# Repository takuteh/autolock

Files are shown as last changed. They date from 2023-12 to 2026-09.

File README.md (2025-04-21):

# オートロック

## GPIO など

リセットボタン（未実装）GPIO 27  
リードスイッチ GPIO 3  
開錠ボタン GPIO 9  
施錠ボタン GPIO 2  
サーボモーター（上側）GPIO 19  
サーボモーター（下側）GPIO 6  
モーター電源用リレー　 GPIO 22

## 運用方法・注意事項

<ins>**1.direct_version(鍵・モーター直結型)**</ins>

- 鍵に直接モーターを取り付けて制御する方式である
  ソースは direct_version 以下

- lock.sh を crontab に記述すれば、起動時に実行されるようになる

- main.py を実行すればオートロックが起動するが、sudo で実行する必要がある

- main.py は C 言語で記述された関数を呼び出しているので、C ディレクトリ内のプログラムを使用する

- ferica 登録は　 read_idm.py 　を実行する、その際他のプログラムなどで
  カードーリーダーを使用していると読み取りができないため全て停止させてから
  読み取りを行う

- 読み取られた idm は idm_list.txt に登録され、プログラムもそのリストから読み出す

- idm_list.txt の一行目がなぜか読み取られないので二行目以降に記述

<ins>**2.gear_version(ギアボックス付きの制御機構)**</ins>

- 施錠・解錠を手動でも行えるようにギアボックス付きのオートロックを追加した
  ソースは `gear_version` 以下

- **セットアップ**
  下記コマンドを実行すれば以下の処理や設定が全て行われる

  ```
  cd gear_version
  mkdir build
  cd build
  cmake ..
  make
  cd ..
  sudo setup.sh
  ```

- **依存関係**  
  `pigpio`,`mosquitto`,`libmosquitto-dev`,`libcurl4-openssl-dev`  
  json は[nlohmann/json](https://github.com/nlohmann/json)ライブラリを使用  
  curl は LINE,Slack の API で使用するため、API を使用しない場合は不要

- **実行ファイル**  
  バイナリは`gear_version/bin`に生成される  
  systemd に autolock のプログラムを登録することで自動起動させることができる  
  Unit ファイルは`gear_version/service/autolock.service`である  
  実行プログラムのパスをバイナリのあるディレクトリに修正する必要あり

- **設定関係**  
  `gear_version/etc/autolock_setting.json`で各種設定を行う  
  以下の各項目について設定が可能である

  - メインの動作設定はオートロックの有無効,ドアの開放時の閉ボタンの動作,鍵の回転方向
    未施錠の場合のタイムアウト秒数,施錠までの秒数を設定する,"no"とすれば無制限
  - MQTT は開錠・施錠・リレー制御のトピック、メッセージ、mqtt ポート、ブローカー ip
  - LINE はチャンネルのアクセストークン、送信先ユーザー ID
  - Slack はチャンネルのアクセストークン、送信先のチャンネル名
  - `/etc/mosquitto/mosquitto.conf`を変更し、mqtt のポート設定と外部からのアクセス許可をする必要あり

- **ライブラリ**  
  外部ライブラリとして`nlohmann/json`,`pigpiod_if2`,`mosquitto`  
  独自ライブラリとして`control_servo`,`min_mqtt`,`autolock_setting`,`line_api`,`slack_api`がある、これらはビルドすると`gear_version/lib`内に配置される  
  `line_api`,`slack_api`は LINE と Slack に通知をするライブラリである

- **テストコード**  
  各種テストコードのビルド先はビルドディレクトリの`src/test_code`内  
  `line_test`と`slack_test`はアクセストークンと送信先をソース内を変更して設定する必要がある  
  `gear_version/src/test_code`内にすべてのソースコードがある  
  作者の環境ではラズパイとモーターの電源は別で取っているので、モーターの動作が不安定になった場合に備えリレーで電源を制御している  
  `reray_on`,`reray_off` でそれぞれ電源の入切が可能である

- サーボモーター MG996R の使用を前提としたギアボックスの 3DCAD データ(stl 形式)は 3D_Models 以下にある

- Eagle で作成した基板データは pcb_data 以下にある([説明](https://github.com/takuteh/autolock/blob/main/pcb_data/READMD.md))

- **API**  
  オートロックの内部 API として MQTT を利用している.
  以下の例のように json 形式でブローカーに目的の動作のトピック名を指定し,メッセージ送信を行う．
  
  **フルメッセージ**
  ```
  {"app":"LINE","message":"1","user":"takuteh"}
  ```

  app,user 要素は，それぞれ通知を行う際にどのアプリから制御を行なったか，誰が操作をしたのかを判別することが可能．
  上記の例で`/door/open`トピックに送信すると`「takutehがLINEで開錠しました」`という通知が行われる.message 要素は必須だが，それ以外は指定しなくても動作する.
  
  **最小構成のメッセージ**
  ```
  {"message":"1"}
  ```

  「unknown が MQTT で開錠しました」という通知が行われる.

  **mosquitto での送信例(broker ip 192.168.1.1 の場合)**
  ```
  mosquitto_pub -h 192.168.1.1 -t "/door/open" -m '{"app":"LINE","message":"1","user":"takuteh"}'
  ```

## ディレクトリ構成

※一部省略

<pre>
autolock/
├── 3D_Models
│   └── ...
├── pcb_data
│   └── ...
├── README.md
├── direct_version
│   ├── C
│   │   ├── Makefile
│   │   ├── close.c
│   │   └── open.c
│   ├── C++
│   │   ├── src
│   │   │   ├── auto_lock.cpp
│   │   │   ├── auto_lock.hpp
│   │   │   ├── switch.cpp
│   │   │   └── switch.hpp
│   │   ├── test
│   │   └── test.cpp
│   ├── Python
│   │   ├── direct_lock.service
│   │   ├── main.py
│   │   └── read_idm.py
│   └── README.txt
└── gear_version
    ├── CMakeLists.txt             :全体のビルド用
    ├── etc
    │   └── autolock_setting.json :設定ファイル
    ├── include                 
    │   ├── autolock_setting.h
    │   ├── control_servo.h
    │   ├── line_api.h
    │   ├── min_mqtt.h
    │   └── slack_api.h
    ├── service
    │   └── autolock.service    :systemdのserviceファイル
    ├── setup.sh                 :初回ビルド前に実行するスクリプト
    └── src
        ├── autolock.cpp         :メインのコード
        ├── autolock_setting.cpp :設定ファイルの読込
        ├── control_servo.cpp    :サーボモーター制御
        ├── line_api.cpp         :LINEへ送信する
        ├── min_mqtt.cpp         :MQTT関連の制御・設定
        ├── slack_api.cpp        :Slackへ送信
        ├── test_code            :デバッグ用コード
        │   ├── CMakeLists.txt  :test_codeのビルド用
        │   ├── down_close.c
        │   ├── down_open.c
        │   ├── line_test.cpp
        │   ├── read_sw.cpp
        │   ├── relay_off.cpp
        │   ├── relay_on.cpp
        │   ├── slack_test.cpp
        │   ├── up_close.c
        │   └── up_open.c
        └── wiringPi_ver
            ├── home_close.c
            ├── home_open.c
            └── lock_open.c
</pre>

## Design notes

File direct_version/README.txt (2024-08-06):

このバージョンは鍵に直接サーボモーターを取り付け制御する方式である

- fericaを使った認証をしたいためライブラリの豊富なPythonがメインのコードである
- サーボモーターの制御自体はCで書いたものを呼び出しているのでC内のopen.c close.cそれぞれをopen closeとしてコンパイルしPythonディレクトリにmvすれば実行可能
- C++はPythonをC++に書き直そうとしているが、開発中のため現在は使用していない
- Pythonディレクトリ内のdirect_lock.serviceを/etc/systemd/system以下に配置すれば、direct_lock.serviceとして登録される

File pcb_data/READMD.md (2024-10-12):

# 基板データ
基板データはAutodesk Eagleにて制作

## 使用部品 (BOM)
調達のしやすい部品を使用しましたが、データシート参照の上、要件を満たす部品に変更しても構いません
### 基板実装
- サーボモーター用コネクタ（[B03B-SXH](https://akizukidenshi.com/catalog/g/g117151/)）×2
- その他コネクタ（[B2B-XH-A-2](https://akizukidenshi.com/catalog/g/g112247/)）×8
- ラズパイ用ピンソケット ([FH-2x20SG](https://akizukidenshi.com/catalog/g/g100085/)) ×1 
- トランジスタ ([2SC1815](https://akizukidenshi.com/catalog/g/g117089/))×1
- 抵抗 100kΩ×4
- 抵抗 1kΩ×1
- ダイオード ([1N4148](https://akizukidenshi.com/catalog/g/g100941/))×1
- リレー ([SRD-05VDC-SL-C](https://www.alldatasheet.jp/datasheet-pdf/pdf/1131944/SONGLERELAY/SRD05VDCSLC.html))×1

### その他
- ラズベリーパイ4
- サーボモーター ([MG996R](https://akizukidenshi.com/catalog/g/g112534/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))
※MG996Rは<b>制御角180°</b>の<b>メタルギア版</b>

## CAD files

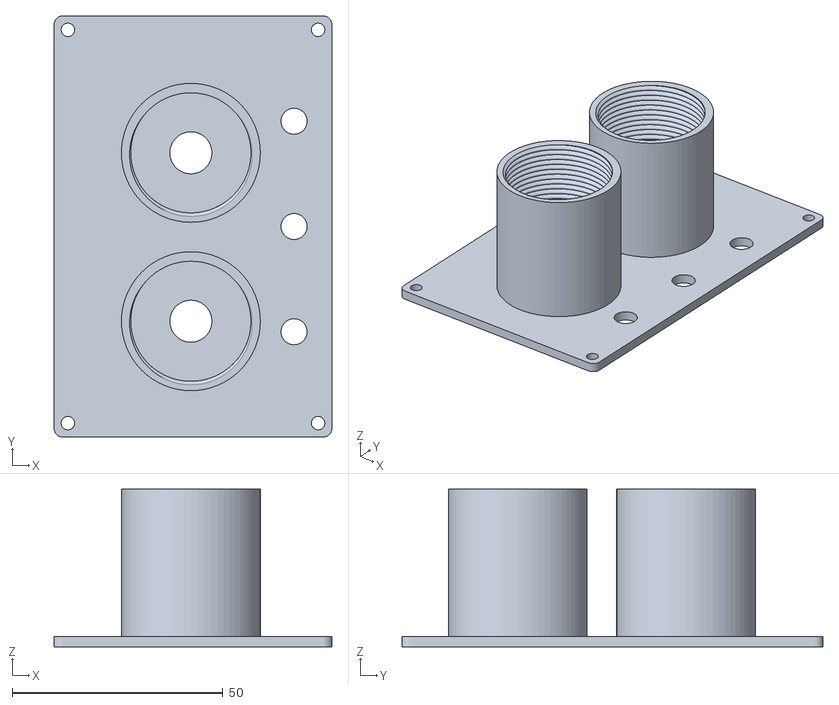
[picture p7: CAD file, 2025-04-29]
3D_Models/RaspiCase_Lid.stl
66.0 x 100.0 x 37.5

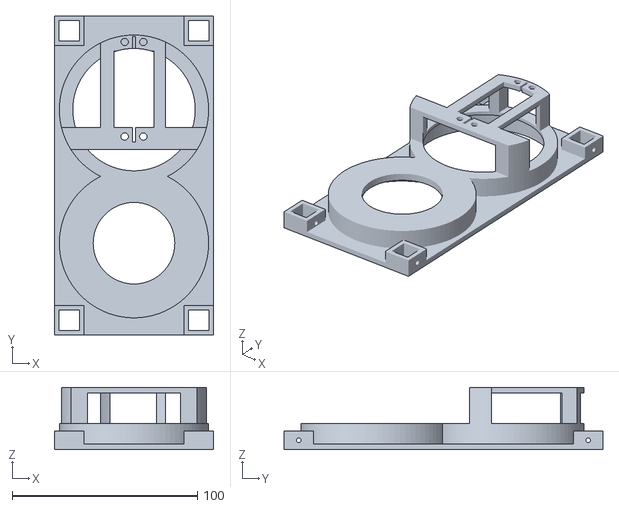
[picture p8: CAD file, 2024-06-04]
3D_Models/GearBox_Lid v8.stl
86.0 x 172.0 x 33.5

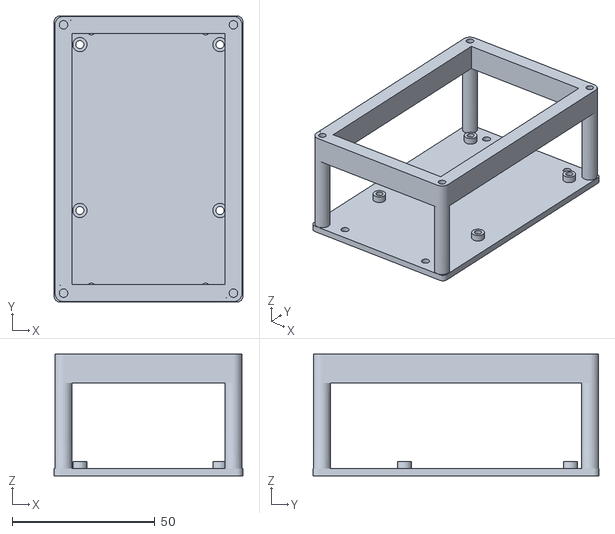
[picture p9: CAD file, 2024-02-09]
3D_Models/RaspiCase_Base v10.stl
66.0 x 100.0 x 42.5

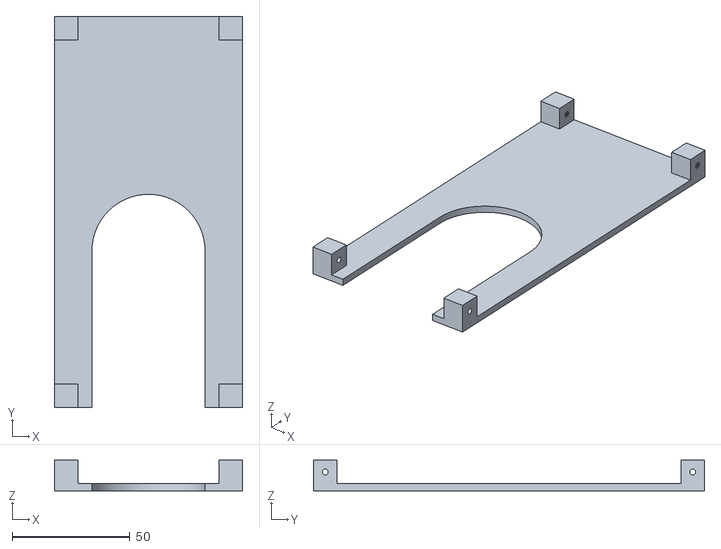
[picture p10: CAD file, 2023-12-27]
3D_Models/GearBox_Base.stl
80.0 x 166.0 x 13.0

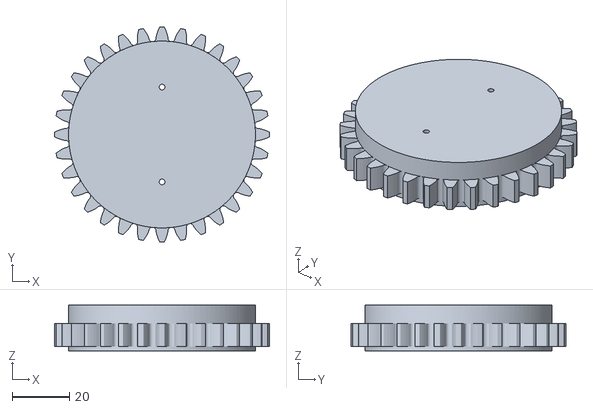
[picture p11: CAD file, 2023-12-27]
3D_Models/Gear_MotorSide.stl
74.8 x 74.8 x 16.0

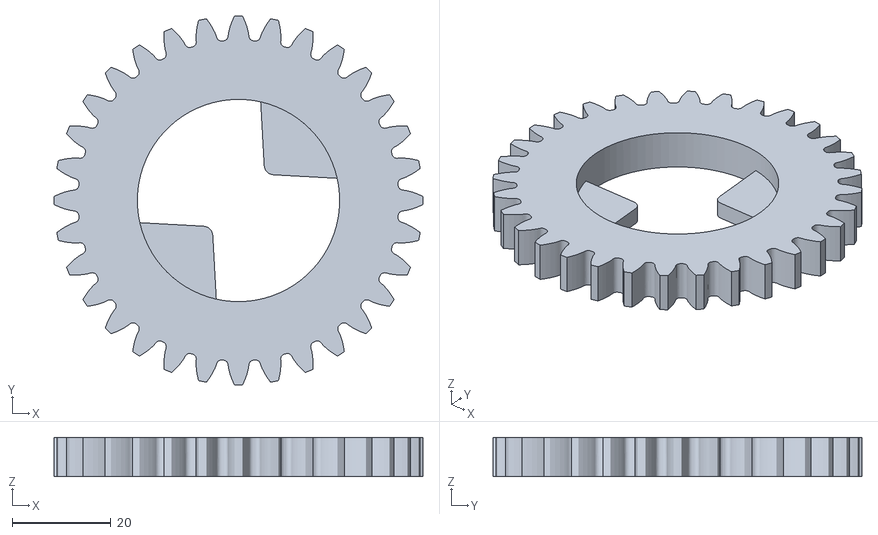
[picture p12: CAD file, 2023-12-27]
3D_Models/Gear_KeySide.stl
74.8 x 74.8 x 8.00

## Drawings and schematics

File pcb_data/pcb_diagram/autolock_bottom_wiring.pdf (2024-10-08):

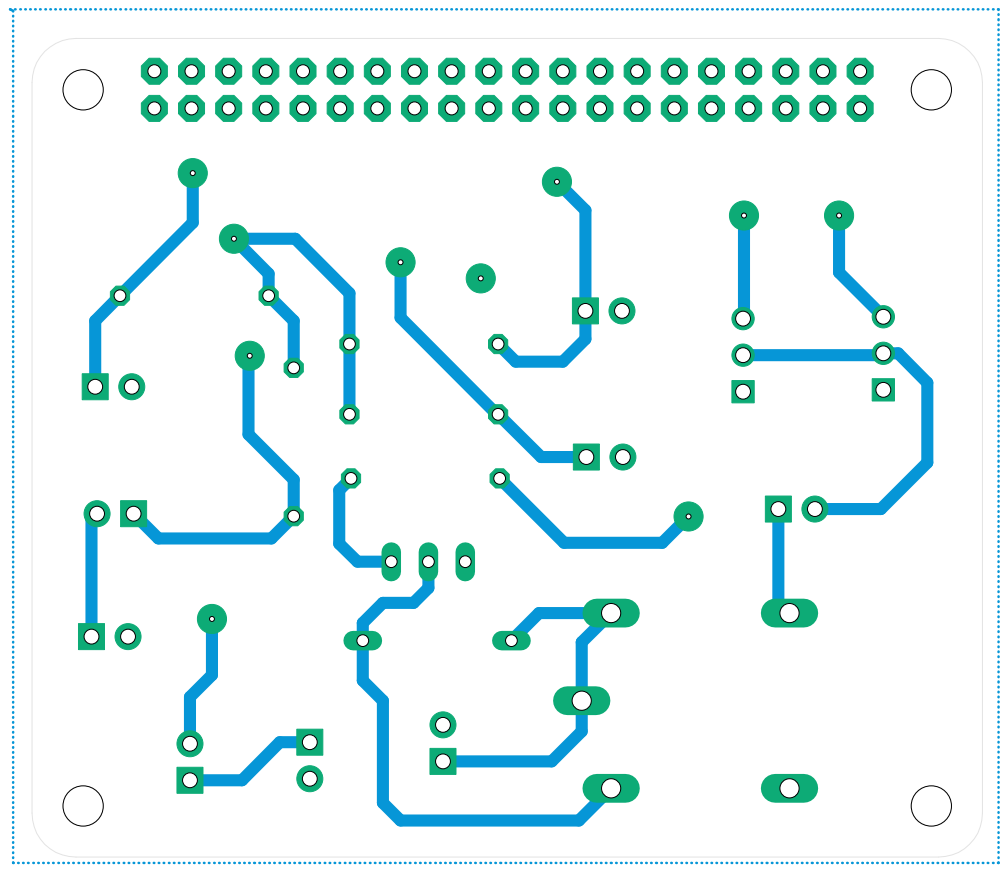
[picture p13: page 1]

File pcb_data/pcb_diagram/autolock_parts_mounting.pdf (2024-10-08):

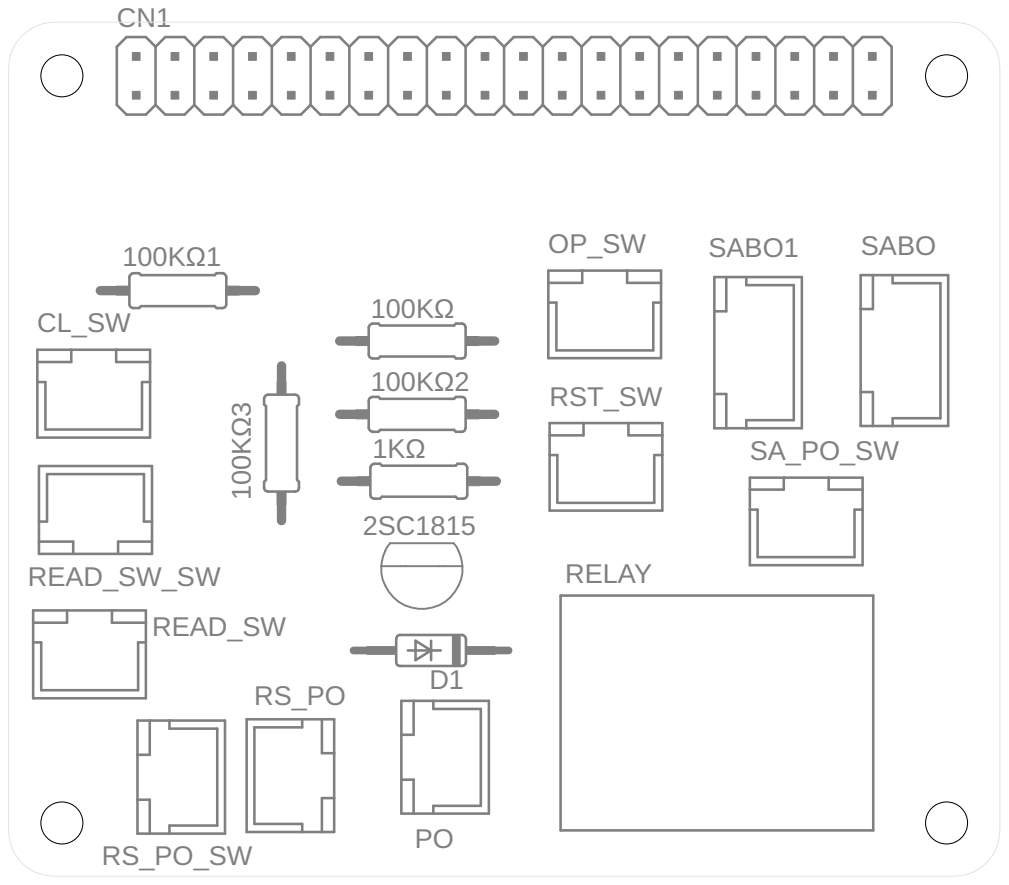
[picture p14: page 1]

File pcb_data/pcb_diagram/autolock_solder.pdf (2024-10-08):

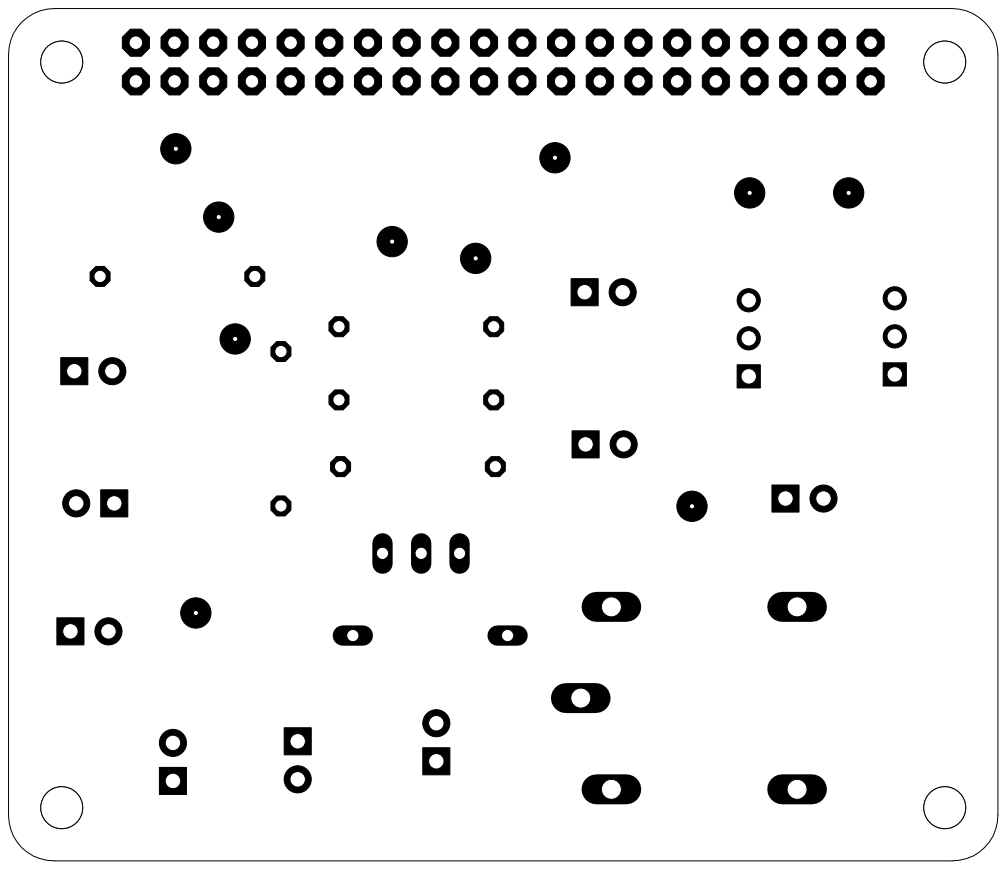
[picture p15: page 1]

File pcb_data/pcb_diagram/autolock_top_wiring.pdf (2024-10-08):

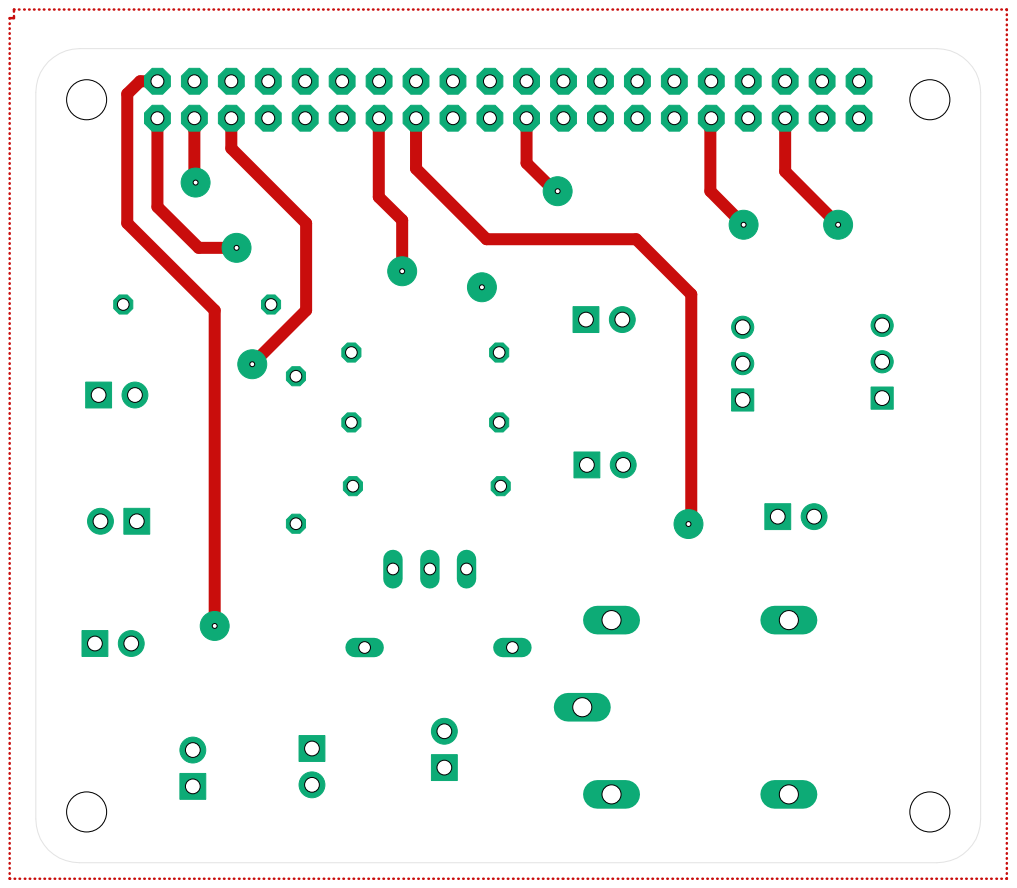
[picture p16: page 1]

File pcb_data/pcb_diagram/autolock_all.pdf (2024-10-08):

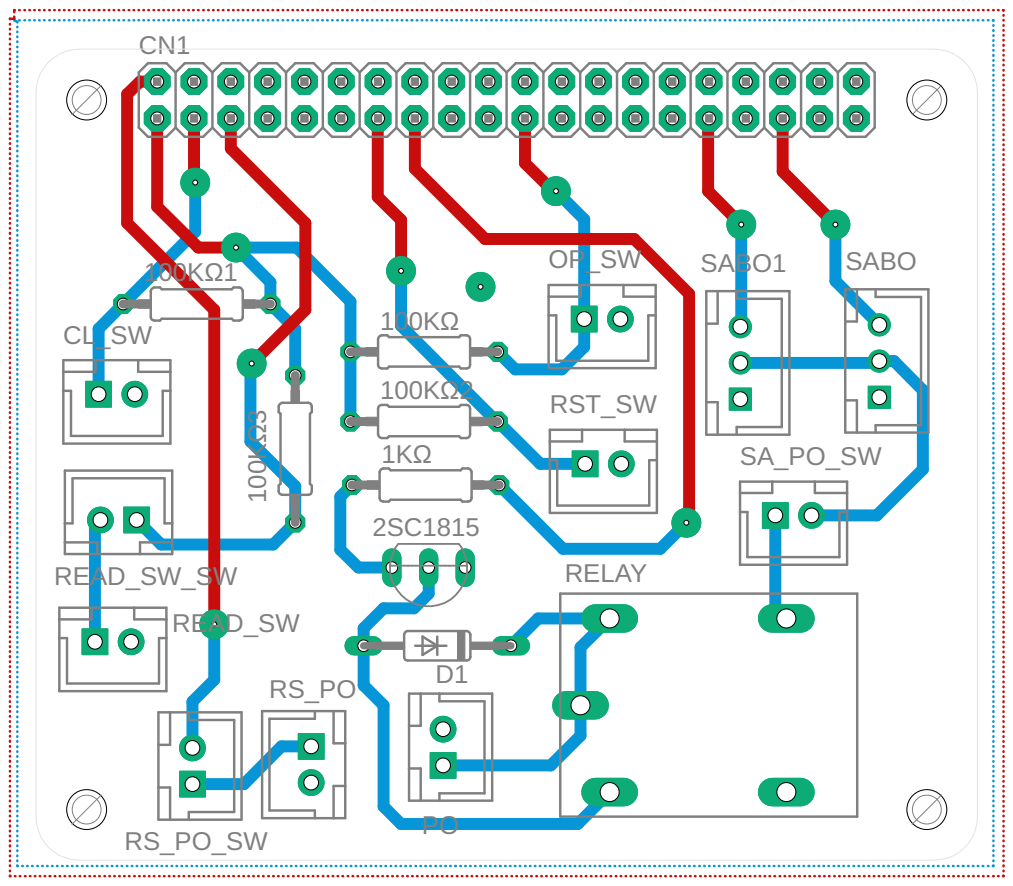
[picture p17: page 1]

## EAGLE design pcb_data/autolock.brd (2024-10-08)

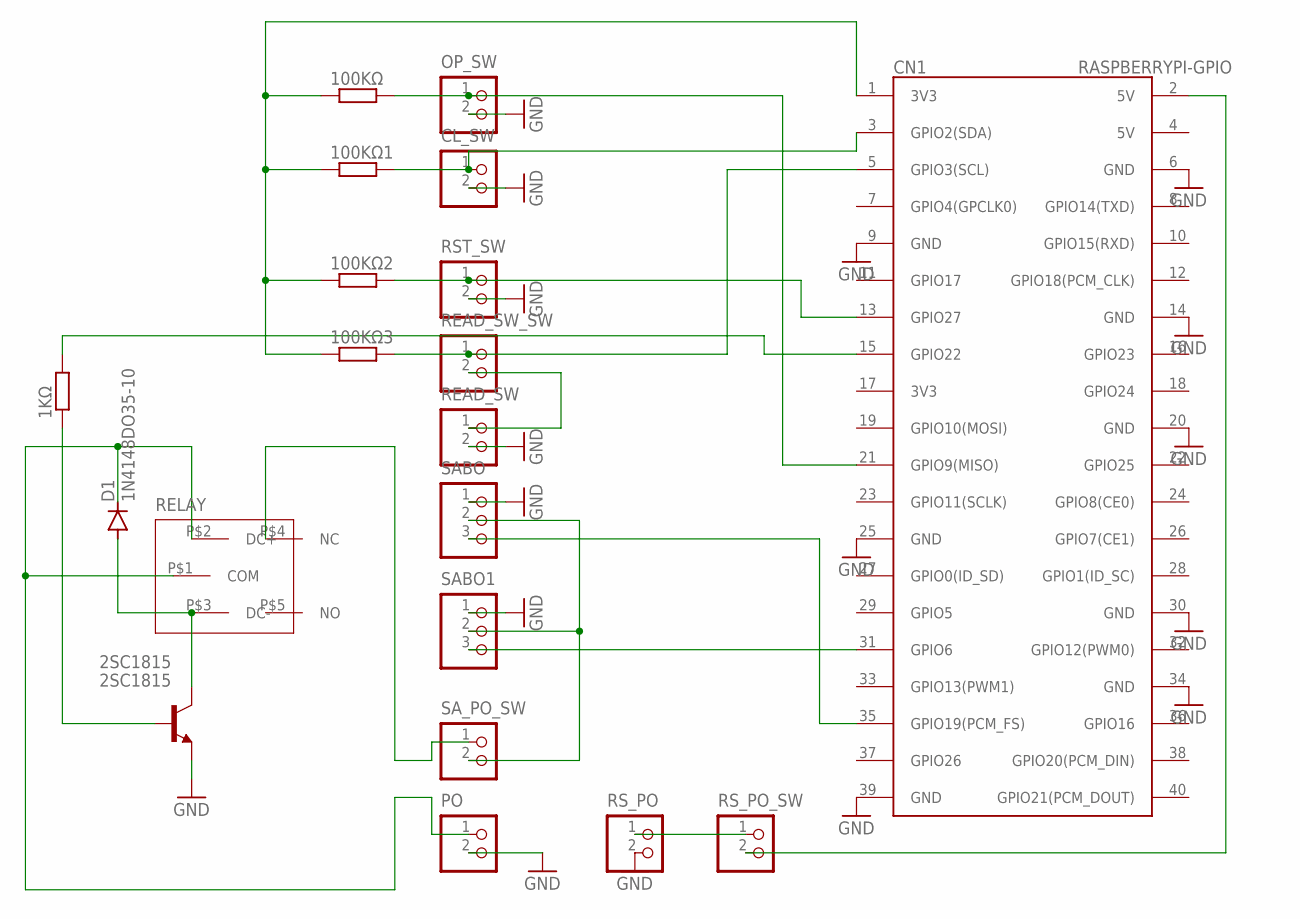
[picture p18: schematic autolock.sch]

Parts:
1KΩ, 100KΩ, 100KΩ1, 100KΩ2, 100KΩ3: R-EU_0207/10; 0207/10
2SC1815: 2SC1815; TO92-ECB
CL_SW: B2B-XH-A
CN1: RASPBERRYPI-GPIO; 2X20-BOLD
D1: 1N4148DO35-10; DO35-10
OP_SW: B2B-XH-A
PO: B2B-XH-A
READ_SW: B2B-XH-A
READ_SW_SW: B2B-XH-A
RELAY: SRD05VDCSLC
RST_SW: B2B-XH-A
RS_PO: B2B-XH-A
RS_PO_SW: B2B-XH-A
SABO, SABO1: B3B-XH-A
SA_PO_SW: B2B-XH-A

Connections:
GND: 2SC1815.E, CL_SW.2, CN1.6 (GND), CN1.9 (GND), CN1.14 (GND), CN1.20 (GND), CN1.25 (GND), CN1.30 (GND), CN1.34 (GND), CN1.39 (GND), OP_SW.2, PO.2, READ_SW.2, RST_SW.2, RS_PO.2, SABO.1, SABO1.1
unnamed: 2SC1815.C, D1.A, RELAY.P$3 (DC-)
unnamed: RS_PO.1, RS_PO_SW.1
unnamed: 100KΩ.1, 100KΩ1.1, 100KΩ2.1, 100KΩ3.1, CN1.1 (3V3)
unnamed: 1KΩ.2, CN1.15 (GPIO22)
unnamed: 100KΩ1.2, CL_SW.1, CN1.3 (GPIO2(SDA))
unnamed: SABO.2, SABO1.2, SA_PO_SW.2
unnamed: CN1.35 (GPIO19(PCM_FS)), SABO.3
unnamed: D1.C, PO.1, RELAY.P$1 (COM), RELAY.P$2 (DC+)
unnamed: CN1.31 (GPIO6), SABO1.3
unnamed: READ_SW.1, READ_SW_SW.2
unnamed: RELAY.P$4 (NC), SA_PO_SW.1
unnamed: CN1.2 (5V), RS_PO_SW.2
unnamed: 1KΩ.1, 2SC1815.B
unnamed: 100KΩ.2, CN1.21 (GPIO9(MISO)), OP_SW.1
unnamed: 100KΩ3.2, CN1.5 (GPIO3(SCL)), READ_SW_SW.1
unnamed: 100KΩ2.2, CN1.13 (GPIO27), RST_SW.1

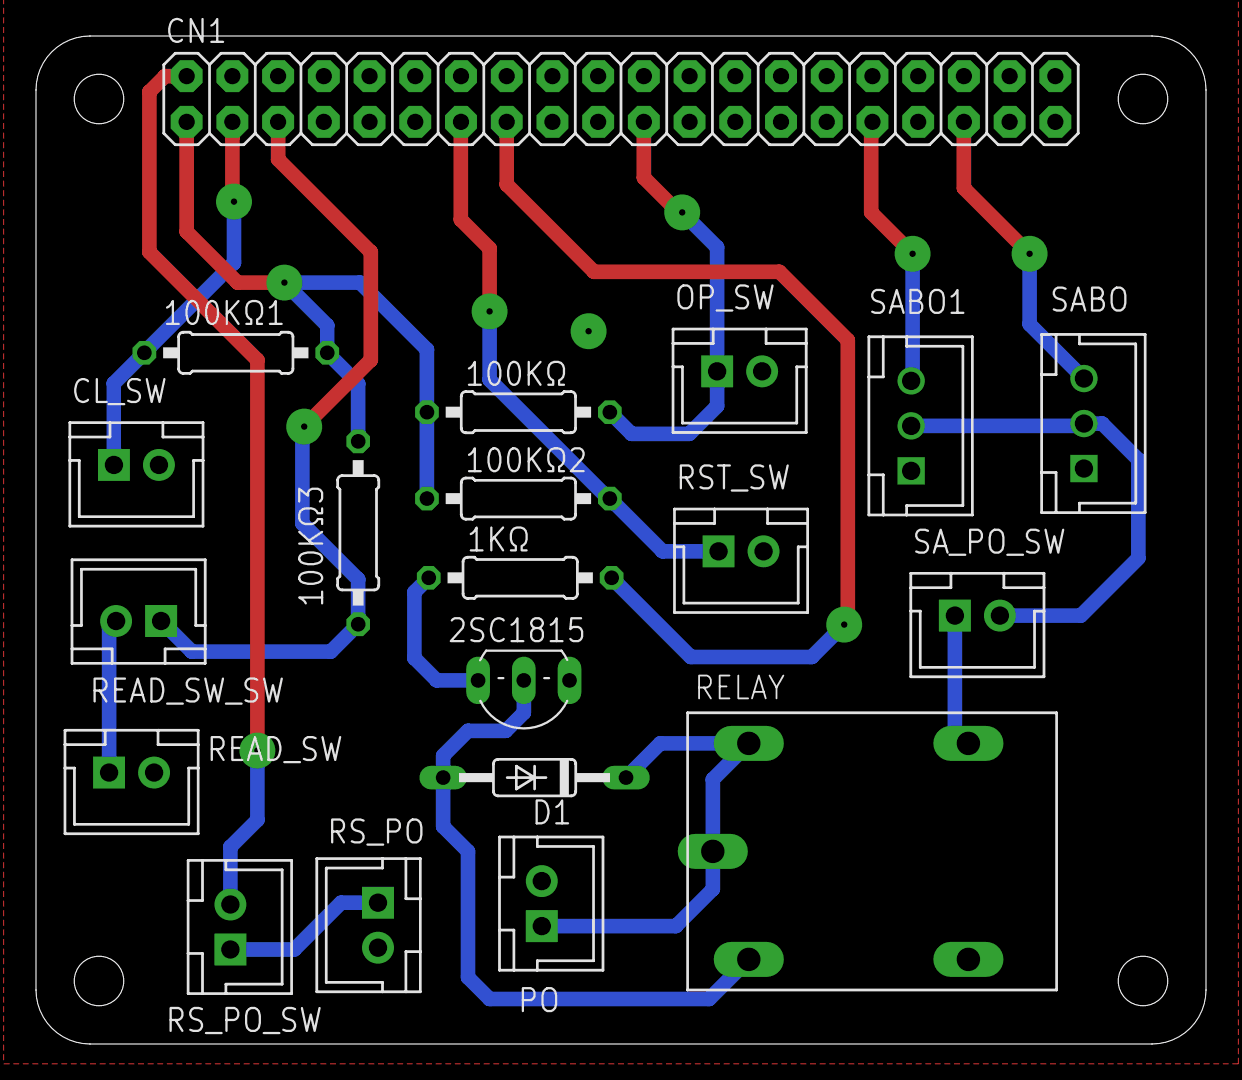
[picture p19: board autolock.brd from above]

Board: 2 copper layers, 65.0 x 56.0 mm, 20 parts (0 on the bottom side), 17 nets.

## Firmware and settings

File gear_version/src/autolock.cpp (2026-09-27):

#include <pigpiod_if2.h>
#include <unistd.h>
#include <iostream>
#include <chrono>
#include <string.h>
#include <thread>
#include <ctime>
#include <nlohmann/json.hpp>
#include <limits>
// 独自ライブラリ
#include <control_servo.h>
#include <min_mqtt.h>
#include <autolock_setting.h>
#include <line_api.h>
#include <slack_api.h>
#include <user_info.h>
#include <authorize_user.h>
#include <change_setting.h>

#define OP_SW 9
#define CL_SW 2
#define RE_SW 3
#define RELAY 22

#define DEBOUNCE_TIME_US 1.5

bool cl_flag = false; // 施錠フラグ
std::string setting_file = MAIN_SETTING_FILE;
int timeout_seq;
int pi = pigpio_start(nullptr, nullptr);

autolock_setting au_set(setting_file);
CONTROL_SERVO autolock(pi, &au_set);
ChangeSetting change_set;
AuthorizeUser authorize_user;
UserInfo user_info;

Mqtt mqtt;
line_api line(au_set.line_channel_token);
slack_api slack(au_set.slack_channel_token);

std::time_t last_rsw_exe_time = 0;     // リードスイッチ、最終処理実行時刻
std::time_t current_rsw_call_time = 0; // リードスイッチ、コールバック呼び出し時刻

void open_sw(int pi, unsigned gpio, unsigned level, uint32_t tick)
{
    if (!autolock.open_switch(level, DEBOUNCE_TIME_US))
    {
        cl_flag = true;
        std::thread([]
                    { 
            //line.send_line_message(au_set.line_user_ids,"ボタンで解錠しました");
            slack.send_slack_message(au_set.slack_log_channel, "ボタンで解錠しました"); })
            .detach();
    }
}

void close_sw(int pi, unsigned gpio, unsigned level, uint32_t tick)
{
    if (!autolock.close_switch(level, DEBOUNCE_TIME_US))
    {
        cl_flag = false;
        std::thread([]
                    { 
            //line.send_line_message(au_set.line_user_ids,"ボタンで施錠しました");
            slack.send_slack_message(au_set.slack_log_channel, "ボタンで施錠しました"); })
            .detach();
    }
}

void read_sw(int pi, unsigned gpio, unsigned level, uint32_t tick)
{
    current_rsw_call_time = time_time(); // 現在時刻の更新
    // 直前のボタンの押下から一定時間が経過していない場合は無視する
    if (current_rsw_call_time - last_rsw_exe_time < DEBOUNCE_TIME_US)
    {
        return;
    }
    if (level == 0)
    {
        std::thread([]
                    {
            //line.send_line_message(au_set.line_user_ids,"ドアが閉まりました");
            slack.send_slack_message(au_set.slack_log_channel, "ドアが閉まりました"); })
            .detach();
        // オートロックが無効なら施錠しない
        if (!au_set.autolock)
        {
            return;
        }
        else if (!autolock.read_switch(level, DEBOUNCE_TIME_US))
        {
            cl_flag = false;
            std::thread([]
                        {
                //line.send_line_message(au_set.line_user_ids,"施錠しました");
                slack.send_slack_message(au_set.slack_log_channel, "施錠しました"); })
                .detach();
            last_rsw_exe_time = time_time(); // 最終処理時刻の更新
        }
    }
    else if (level == 1)
    {
        std::thread([]
                    { 
            //line.send_line_message(au_set.line_user_ids,"ドアが開きました");
            slack.send_slack_message(au_set.slack_log_channel, "ドアが開きました"); })
            .detach();
        last_rsw_exe_time = time_time(); // 最終処理時刻の更新
    }
}

void mqtt_message_received_wrapper(struct mosquitto *mosq, void *userdata, const struct mosquitto_message *message)
{
    std::string topic_str = message->topic;
    std::string payload_str = (char *)message->payload;
    std::cout << topic_str << std::endl;

    nlohmann::json mqtt_mes = nlohmann::json::parse(payload_str);

    // 送信メッセージ定義
    std::string send_str = "";
    user_info.user_name = mqtt_mes.value("user", "Unknown");
    user_info.line_user_id = mqtt_mes.value("line_id", "null");
    user_info.slack_user_id = mqtt_mes.value("slack_id", "null");

    std::string app = mqtt_mes.value("app", "MQTT");
    std::string operate_mes = mqtt_mes.value("message", "null");

    bool is_authorized = false;
    bool is_registered = false;
    if (app == "MQTT") // 内部からの通信の場合
    {
        if (au_set.authorize_internal_users)
        {
            std::pair<bool, bool> result = authorize_user.authorize(user_info, app);
            is_authorized = result.first;
            is_registered = result.second;
        }
        else
        {
            is_authorized = true;
        }
    }
    else // 外部からの通信の場合
    {
        if (au_set.authorize_external_users)
        {
            std::pair<bool, bool> result = authorize_user.authorize(user_info, app);
            is_authorized = result.first;
            is_registered = result.second;
        }
        else
        {
            is_authorized = true;
        }
    }

    std::string operation = "";
    bool send_flag = false; // 送信フラグ
    if (topic_str == au_set.change_conf_topic)
    {
        if (is_authorized)
        {
            operation = "設定変更";
            if (change_set.apply_setting(MAIN_SETTING_FILE, mqtt_mes["setting_content"]))
            {
                mosquitto_publish(mqtt.mosq, NULL, au_set.boot_topic, au_set.load_setting().size(), au_set.load_setting().c_str(), 1, false);
            }
            else
            {
                operation = "設定変更に失敗";
            }
        }
        send_flag = true;
    }

    if (topic_str == au_set.open_topic && operate_mes == au_set.open_message)
    {
        if (is_authorized)
        {
            autolock.open_switch(1, DEBOUNCE_TIME_US);
            cl_flag = true;
        }
        send_flag = true;
        operation = "解錠";
    }

    if (topic_str == au_set.close_topic && operate_mes == au_set.close_message)
    {
        if (is_authorized)
        {
            autolock.close_switch(1, DEBOUNCE_TIME_US);
            cl_flag = false;
        }
        send_flag = true;
        operation = "施錠";
    }

    if (topic_str == au_set.relay_on_topic && operate_mes == au_set.relay_on_message)
    {
        if (is_authorized)
        {
            std::cout << "relay_on" << std::endl;
            gpio_write(pi, RELAY, 1);
        }
        send_flag = true;
        operation = "モーターオフ";
    }

    if (topic_str == au_set.relay_off_topic && operate_mes == au_set.relay_off_message)
    {
        if (is_authorized)
        {
            std::cout << "relay_off" << std::endl;
            gpio_write(pi, RELAY, 0);
        }
        send_flag = true;
        operation = "モーターオン";
    }

    if (send_flag)
    {
        if (is_authorized)
        {
            send_str = user_info.user_name + "が" + app + "で" + operation + "しました";
        }
        else
        {
            std::string auth_status;
            if (is_registered)
            {
                auth_status = "期限切れ";
            }
            else
            {
                auth_status = "未登録";
            }
            send_str = auth_status + "のユーザー" + user_info.user_name + "が" + app + "で" + operation + "を試みました。user idは"+ user_info.line_user_id +"です。";
        }
        std::cout << send_str << std::endl;
        // line.send_line_message(au_set.line_user_ids, send_str);
        slack.send_slack_message(au_set.slack_log_channel, send_str);
        slack.send_slack_message(au_set.slack_app_operate_notify_channel, send_str);
        send_flag = false;
    }
}
int main()
{
    //  mqttの設定
    mqtt.mosq = mosquitto_new(NULL, true, NULL);
    mqtt.initialize_mqtt(au_set);

    mosquitto_message_callback_set(mqtt.mosq, mqtt_message_received_wrapper);

    set_mode(pi, OP_SW, PI_INPUT);
    set_mode(pi, CL_SW, PI_INPUT);
    set_mode(pi, RE_SW, PI_INPUT);
    set_mode(pi, RELAY, PI_OUTPUT);

    // 各ボタンをプルダウンに設定
    set_pull_up_down(pi, OP_SW, PI_PUD_UP);
    set_pull_up_down(pi, CL_SW, PI_PUD_UP);
    set_pull_up_down(pi, RE_SW, PI_PUD_UP);
    set_pull_up_down(pi, RELAY, PI_PUD_DOWN);

    // ボタン割り込みのコールバック関数設定
    callback(pi, OP_SW, RISING_EDGE, open_sw);
    callback(pi, CL_SW, RISING_EDGE, close_sw);
    callback(pi, RE_SW, EITHER_EDGE, read_sw);

    mosquitto_loop_start(mqtt.mosq);

    // 起動通知の送信
    mosquitto_publish(mqtt.mosq, NULL, au_set.boot_topic, au_set.load_setting().size(), au_set.load_setting().c_str(), 1, false);
    slack.send_slack_message(au_set.slack_log_channel, "オートロックが起動しました");

    while (1)
    {
        autolock.current_rsw_time = time_time();
        auto elapsed_rsw_time = autolock.current_rsw_time - autolock.start_rsw_time;
        // 鍵が開きっぱなしにならないための処理
        if (au_set.timeout_seq != "no" && au_set.autolock)
        {
            timeout_seq = stoi(au_set.timeout_seq);
            if (cl_flag == true && elapsed_rsw_time >= timeout_seq)
            {
                // ドアが閉まっているかの確認
                if (gpio_read(pi, RE_SW) == 0)
                {
                    std::cout << "door_closed" << std::endl;
                    autolock.close(19, 6);
                    cl_flag = false;
                    std::thread([]
                                {
                    //line.send_line_message(au_set.line_user_ids, "タイムアウトしたため施錠しました");
                    slack.send_slack_message(au_set.slack_log_channel, "タイムアウトしたため施錠しました"); })
                        .detach();
                }
            }
        }
        sleep(1);
        std::cout << gpio_read(pi, RE_SW) << std::endl;
    }
    mqtt.clean_mqtt();
    return 0;
}

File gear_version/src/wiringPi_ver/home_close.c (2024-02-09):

#include <stdio.h>
#include <stdint.h>
#include <wiringPi.h>

#define SERVO_PIN 19

int main(){
  if (wiringPiSetupGpio() == -1) {
     printf("cannot setup gpio.");
    return 1;
  }

  pinMode(SERVO_PIN, PWM_OUTPUT);
  pwmSetMode(PWM_MODE_MS);
  pwmSetClock(400);
  pwmSetRange(1024);
   
     pwmWrite(SERVO_PIN,70);
delay(100);
     pwmWrite(SERVO_PIN,20);
delay(800);
     pwmWrite(SERVO_PIN,70); 

  return 0;
}

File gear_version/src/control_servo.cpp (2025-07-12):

#include <pigpiod_if2.h>
#include <control_servo.h>
#include <chrono>
#include <iostream>

#define RE_SW 3

CONTROL_SERVO::CONTROL_SERVO(int pi, autolock_setting *au_set)
{
    this->pi = pi;
    this->au_set = au_set;
}

CONTROL_SERVO::~CONTROL_SERVO()
{
    pigpio_stop(this->pi);
}

// モーターを右方向に回転させる
void CONTROL_SERVO::rotate_right(int gpio_pin1, int gpio_pin2)
{
    set_servo_pulsewidth(this->pi, gpio_pin1, 1500);
    set_servo_pulsewidth(this->pi, gpio_pin2, 1500);
    usleep(100000);
    set_servo_pulsewidth(this->pi, gpio_pin1, 500);
    set_servo_pulsewidth(this->pi, gpio_pin2, 500);
    usleep(800000);
    set_servo_pulsewidth(this->pi, gpio_pin1, 1500);
    set_servo_pulsewidth(this->pi, gpio_pin2, 1500);
}
// モーターを左方向に回転させる
void CONTROL_SERVO::rotate_left(int gpio_pin1, int gpio_pin2)
{
    set_servo_pulsewidth(this->pi, gpio_pin1, 1500);
    set_servo_pulsewidth(this->pi, gpio_pin2, 1500);
    usleep(100000);
    set_servo_pulsewidth(this->pi, gpio_pin1, 2500);
    set_servo_pulsewidth(this->pi, gpio_pin2, 2500);
    usleep(800000);
    set_servo_pulsewidth(this->pi, gpio_pin1, 1500);
    set_servo_pulsewidth(this->pi, gpio_pin2, 1500);
}

void CONTROL_SERVO::open(int gpio_pin1, int gpio_pin2)
{
    if (this->au_set->rotate_direction == "left")
    {
        this->rotate_left(gpio_pin1, gpio_pin2);
    }
    else if (this->au_set->rotate_direction == "right")
    {
        this->rotate_right(gpio_pin1, gpio_pin2);
    }
}

void CONTROL_SERVO::close(int gpio_pin1, int gpio_pin2)
{
    if (this->au_set->rotate_direction == "left")
    {
        this->rotate_right(gpio_pin1, gpio_pin2);
    }
    else if (this->au_set->rotate_direction == "right")
    {
        this->rotate_left(gpio_pin1, gpio_pin2);
    }
}

int CONTROL_SERVO::open_switch(unsigned level, float debounce_time)
{
    this->current_time = time_time();
    // 直前のボタンの押下から一定時間が経過していない場合は無視する
    if (this->current_time - this->last_button_time < debounce_time)
    {
        return 1;
    }
    if (level == 1)
    {
        this->start_rsw_time = time_time();
        std::cout << "open" << std::endl;
        this->open(19, 6);
    }
    // 最後のボタン押下時刻を更新
    this->last_button_time = this->current_time;
    return 0;
}

int CONTROL_SERVO::close_switch(unsigned level, float debounce_time)
{
    this->current_time = time_time();
    // 直前のボタンの押下から一定時間が経過していない場合は無視する
    if (this->current_time - this->last_button_time < debounce_time)
    {
        return 1;
    }
    if (level == 1)
    {
        if (gpio_read(pi, RE_SW) == 1 && this->au_set->ignore_clsw)
        { // リードセンサーに反応がない場合無視する
            std::cout << "The door is open so ignore it" << std::endl;
            return 1;
        }
        std::cout << "close" << std::endl;
        this->close(19, 6);
    }
    // 最後のボタン押下時刻を更新
    this->last_button_time = this->current_time;
    return 0;
}

int CONTROL_SERVO::read_switch(unsigned level, float debounce_time)
{
    if (level == 0)
    {
        std::cout << "read_sw" << std::endl;
        sleep(2); // 完全に扉が閉まるまで待機
        this->close(19, 6);
    }
    return 0;
}

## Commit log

2023-08-13 pythonでは一通り機能が完成している
2023-12-27 ギアボックス機構追加
    [GearBox_Base.stl, GearBox_Lid.stl, Gear_KeySide.stl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]
2024-01-31 サーボモーターコード修正
2024-02-09 基板・ケースデータ追加
    [autolock.brd, autolock.sch, lock_raspibase v10.stl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]
2024-02-10 pigpioでサーボモーター制御を書き直した
2024-02-11 割り込み完成・ディレクトリ整理
2024-02-19 基板修正・リードスイッチ調整
    [autolock.brd, autolock.sch]
2024-02-25 mqtt実装・基板修正
2024-04-02 リレーの制御を追加
2024-06-04 Makefile追加・README修正
2024-06-04 3Dmodel・README修正
    [lock_raspilid v7.stl, lock_raspilid v8.stl]
2024-06-08 setup.sh追加、unitファイル修正
2024-06-11 不要なファイルを削除
2024-07-27 CMake追加、ファイル読込部分修正
2024-07-30 test_code関連cmake化
2024-08-06 direct_version、C修正
2024-08-17 LINEに通知＆設定読み込み変更
2024-08-18 リードスイッチ周り修正
2024-08-21 api部分修正＆slack api追加
2024-08-21 設定項目追加・mainスレッド処理修正
2024-08-25 main施錠通知追加・APIテストコード追加
2024-08-25 README修正
2024-08-28 施錠フラグ追加、タイムアウト処理改良
2024-08-28 mqttメッセージjson化
2024-08-28 不要なMakefile削除
2024-08-28 READMEディレクトリ構成追記
2024-10-07 基板データ修正
    [autolock.brd, autolock.sch]
2024-10-07 serviceファイル修正,after->mosquitto
2024-10-08 基板GND周り修正、実装図追加
    [autolock.brd, autolock.sch]
2024-10-12 PCB用README作成
2024-11-23 test_code,relay_offをCMakeに追加
2024-12-13 setup.sh mqtt追記されてしまう問題修正
2024-12-13 setup.sh aptオプションy,cmake追加
2025-03-30 施錠までのタイムアウトを設定ファイルから設定するように変更
2025-04-20 pthreadライブラリのリンクを追加
2025-04-20 回転方向を設定項目に追加
2025-04-21 オートロックの有効・無効を設定に追加
2025-04-21 ドアが空いている際にclose swを無視するかを設定項目に追加
2025-04-29 setting.jsonコメント削除
2025-04-29 3Dmodel修正
    [GearBox_Lid v8.stl, GearBox_Lid.stl, RaspiCase_Base v10.stl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]
2025-07-04 setting.jsonの形式変更，mqtt受信処理をループに変更
2025-07-12 dbの認証を通すように変更
2025-07-12 認証を行うかどうかの設定を追加
2025-07-12 オートロックの有効化，リードセンサーの無視の設定をbool型に変更
2025-07-13 ユーザー認証に時刻の比較を追加
2025-07-13 設定変更用のトピックを追加
2025-07-13 設定再読み込み用の処理を追加
2025-07-13 mqttで設定変更をできるように変更
2025-07-13 モーターリセットをオンとオフに分割
2025-07-13 不要な部分を削除
2025-07-15 認証周りのバグ修正
2025-07-15 不要なトピックの処理を削除
2025-07-16 起動時に設定内容をmqttで送信できるようにした
2025-07-19 appで操作したときのみ別のチャンネルにも送信できるようにした
2025-07-19 認証する際app名を小文字に直すように修正
2025-08-17 権限のないユーザーの操作通知にline idを入れるように変更
